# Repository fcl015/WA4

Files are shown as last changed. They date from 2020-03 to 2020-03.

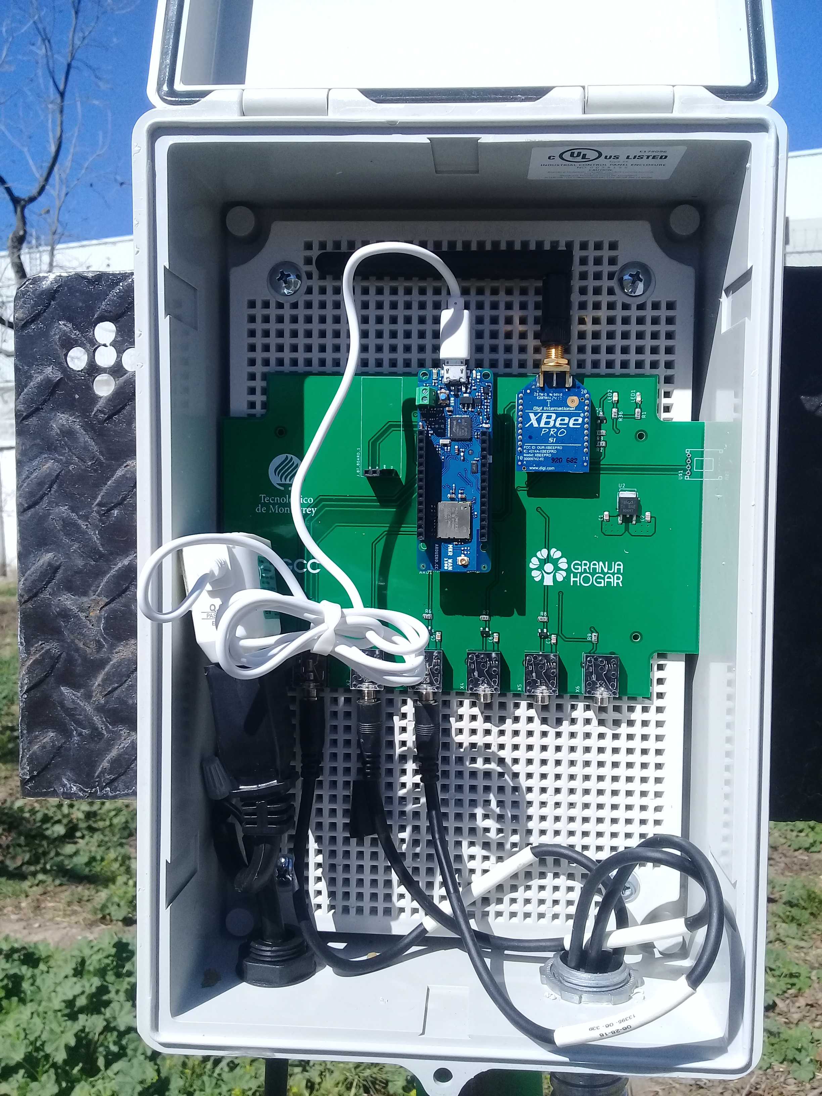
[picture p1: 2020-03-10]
03_Documentos/Fotos/2019-01/20190207_122751.jpg

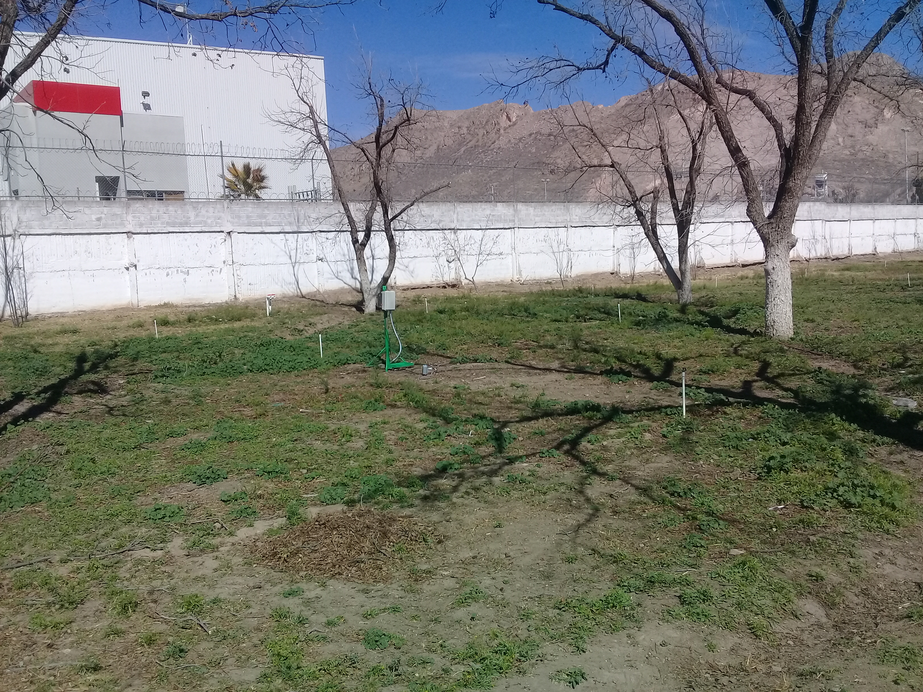
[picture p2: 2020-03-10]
03_Documentos/Fotos/2019-01/20190207_122912.jpg

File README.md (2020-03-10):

# WA4

Plataforma Tecnológica para Riego de Precisión
Se ha desarrollado y validado en campo una plataforma tecnológica para el manejo eficiente en la distribución y el consumo de agua en sistemas de riego agrícola y de áreas verdes. La plataforma ofrece servicios de internet de las cosas, medición, control, predicción y supervisión para una red de riego inteligente capaz de manejar restricciones de infraestructura (agua y energía limitada) valorando las condiciones ambientales (radiación solar, temperatura, lluvia, evapotranspiración) y del cultivo (humedad de suelo, desarrollo vegetativo).  
Actualmente la plataforma se encuentra instalada en una huerta Nogalera y en un invernadero. Experimentalmente, se han obtenido resultados de ahorro de agua entre 30%-40% y de reducción de consumo de energía de entre 20%-30% con respecto a los sistemas de riego automatizados utilizados en la región.
La plataforma consta de tres productos: (1) Crop.Net para monitoreo de humedad de suelo y desarrollo vegetativo, (2) Weather.Net para monitoreo de condiciones ambientales, y (3) Water.Net para control de riego y fertilizantes. Estos productos son modulares y escalables para ajustarse a las necesidades del cliente y al tamaño de las áreas de cultivo.

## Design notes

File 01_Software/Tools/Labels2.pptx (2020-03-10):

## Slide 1

Nodo Climático
Xbee: 0013A20040B135BC
Bluetooth: CLIMA

Nodo Sensor
Xbee: 0013A200416CC8A3
Bluetooth: AREA01

Nodo Sensor
Xbee: 0013A200416CC89C
Bluetooth: AREA02

Nodo Sensor
Xbee: 0013A200416CC899
Bluetooth: AREA03

Nodo Sensor
Xbee: 0013A200416CC89B
Bluetooth: AREA04

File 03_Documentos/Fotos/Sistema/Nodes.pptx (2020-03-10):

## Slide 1

Unidad Microcontroladora
SAMD21 Cortex-M0+ 32bit low power ARM

Blue-tooth
comm

Fuente de Poder

Zigbee comm

Nodo Sensor

LoRa comm

GPS

Unidad Microcontroladora
SAMD21 Cortex-M0+ 32bit low power ARM

Blue-tooth
comm

Fuente de Poder

Zigbee comm

Nodo Actuador

LoRa comm

GPS

Acondicio-namiento de entrada

Acondicio-namiento de entrada

Acondicio-namiento de salida

Sensor 1

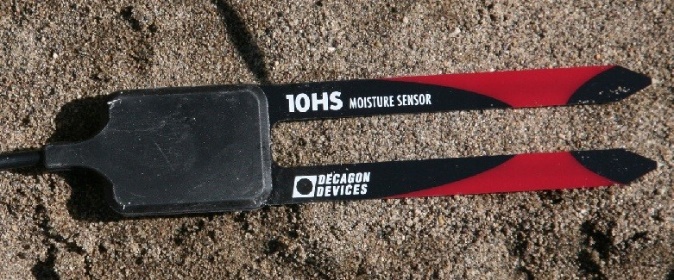
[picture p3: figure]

Sensor Flujo

Válvula

Sensor 2

Sensor 3

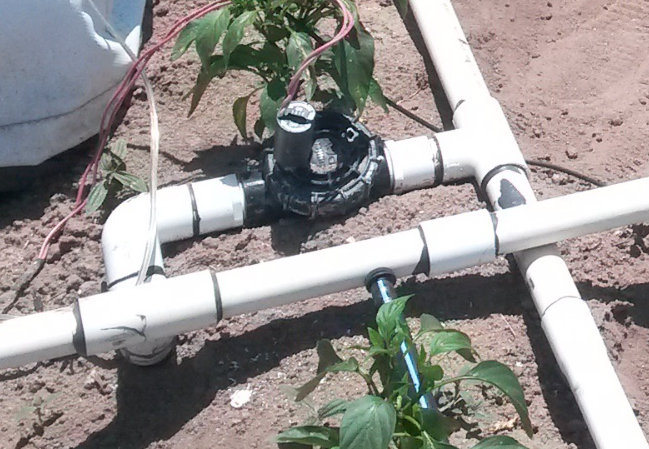
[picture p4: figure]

NDVI field

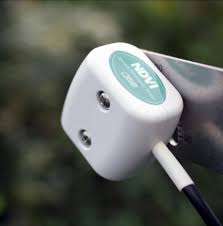
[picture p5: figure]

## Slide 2

Unidad Microcontroaldora
SAMD21 Cortex-M0+ 32bit low power ARM

Nodo Climático

LoRa comm

Nodo Controlador

Raspberry Pi 3B+
(Bradcom BCM2837Bo quad-core A53, 64bits, 1.4 GHz)

Blue-tooth
comm

Fuente de Poder

Zigbee comm

GPS

Blue-tooth
comm

Fuente de Poder

Zigbee comm

NIR Camera

WiFi
comm

Acondicio-namiento de entrada

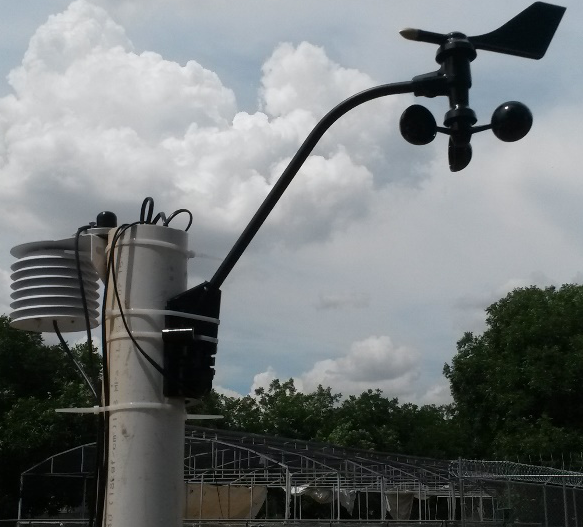
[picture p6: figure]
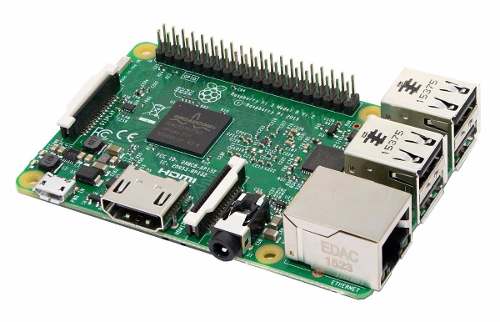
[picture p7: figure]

Davis Cup

PYR Sensor

NDVI Hem

VP-4

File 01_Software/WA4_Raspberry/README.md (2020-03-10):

# WA4_Raspberry
# Updated Sep-2019

Directories:

bin 	- python executable programs
config 	- csv configuration files
data 	- latest data from sensors and actuators
log 	- output log files
scripts - scripts for crontab and boot
tools	- program tools to check communication with nodes
www	- web interface (OLD webiopi)
www_flask - web interface (NEW flask)

Files

bin\control_loop_area1.py	- main file for irrigation area 1
bin\control_loop_area2.py	- main file for irrigation area 2
bin\control_loop_area3.py	- main file for irrigation area 3
bin\control_loop_area4.py	- main file for irrigation area 4
bin\wa_config_data.py		- functions to access configuration files
bin\wa_control.py		- functions for control and data fusion algorithms
bin\wa_xbee_comm.py		- function for Zigbee communication
bin\wa_iot_comm.py		- function for IoT interface (ThingSpeak)

config\config_area1.csv		- configuration file for irrigation area 1
config\config_area2.csv		- configuration file for irrigation area 2
config\config_area3.csv		- configuration file for irrigation area 3
config\config_area4.csv		- configuration file for irrigation area 4
config\manual_control_area1.csv	- configuration file for manual irrigation area 1
config\manual_control_area2.csv	- configuration file for manual irrigation area 2
config\manual_control_area3.csv	- configuration file for manual irrigation area 3
config\manual_control_area4.csv	- configuration file for manual irrigation area 4
config\sched_area1.csv		- configuration file for scheduling irrigation area 1
config\sched_area2.csv		- configuration file for scheduling irrigation area 2
config\sched_area3.csv		- configuration file for scheduling irrigation area 3
config\sched_area4.csv		- configuration file for scheduling irrigation area 4
config\operation_mode_area1.csv	- confirguration file for operation mode area 1
config\operation_mode_area2.csv	- confirguration file for operation mode area 2
config\operation_mode_area3.csv	- confirguration file for operation mode area 3
config\operation_mode_area4.csv	- confirguration file for operation mode area 4

log\crontab.txt			- log data for coontab services
log\video.txt			- log data for video server
log\webiopi.txt			- log data for webiopi server
log\webfalsk.txt		- log data for flask server

scripts\cron.txt		- cron process definition, start each irrigation area monitoring every 5 minutes
scripts\start_crontab.sh	- script to start crontab process (once executed, onlye removed by command. crontab -r
scripts\start_mjpg_streamer.sh	- start video server during startup (boot), to configure file must be copied to directory /etc/init.d/
scripts\start_webiopi.sh	- (OLD)start web server during startup (boot), to configure file must be copied to directory /etc/init.d/
scripts\start_WebFlaskServer.sh	- (NEW)start web falsk server during startup (boot), to configure file must be copied to directory /etc/init.d/
scripts\start_WA4_Raspberry_All_Areas.sh	-execute monitor and control for all areas
scripts\start_WA4_Raspberry_Area1.sh		-execute monitor and control for area 1
scripts\start_WA4_Raspberry_Area2.sh		-execute monitor and control for area 2
scripts\start_WA4_Raspberry_Area3.sh		-execute monitor and control for area 3
scripts\start_WA4_Raspberry_Area4.sh		-execute monitor and control for area 4

tools\actuator_message.py	- Program to check communication with actuator node
tools\sensor_message.py		- Program to check communication with sensor node
tools\weather_message.py	- Program to check communication with weather node

www\html\			- (OLD) webiopi web pages for WA interface
www\python\scripts.py		- (OLD) main script to extract data from config, data and scripts directories

www\html\log_area1.csv		- output log data for irrigation area 1
www\html\log_area2.csv		- output log data for irrigation area 2
www\html\log_area3.csv		- output log data for irrigation area 3
www\html\log_area4.csv		- output log data for irrigation area 4

www_flask\runWebServer.py	- (NEW) Main flask program
www_flask\wa4_functions.py	- (NEW) Complementary flask functions
www_flask\static\		- (NEW) Javascript and css files
www_flask\templates\		- (NEW) HTML files for flask

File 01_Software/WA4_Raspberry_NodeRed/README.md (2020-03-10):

# WA4_Raspberry
# Updated Sep-2019

Directories:

bin 	- python executable programs
config 	- csv configuration files
data 	- latest data from sensors and actuators
log 	- output log files
scripts - scripts for crontab and boot
tools	- program tools to check communication with nodes
www_flask - web interface

Files

bin\control_loop_area1.py	- main file for irrigation area 1
bin\control_loop_area2.py	- main file for irrigation area 2
bin\control_loop_area3.py	- main file for irrigation area 3
bin\control_loop_area4.py	- main file for irrigation area 4
bin\wa_config_data.py		- functions to access configuration files
bin\wa_control.py		- functions for control and data fusion algorithms
bin\wa_xbee_comm.py		- function for Zigbee communication
bin\wa_iot_comm.py		- function for IoT interface (ThingSpeak)

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

data\data_area1.csv		- Current data for irrigation area 1
data\data_area2.csv		- Current data for irrigation area 2
data\data_area3.csv		- Current data for irrigation area 3
data\data_area4.csv		- Current data for irrigation area 4

log\crontab.txt			- log data for coontab services
log\video.txt			- log data for video server
log\webiopi.txt			- log data for webiopi server
log\webfalsk.txt		- log data for flask server

scripts\cron.txt		- cron process definition, start each irrigation area monitoring every 5 minutes
scripts\start_crontab.sh	- script to start crontab process (once executed, onlye removed by command. crontab -r
scripts\start_mjpg_streamer.sh	- start video server during startup (boot), to configure file must be copied to directory /etc/init.d/
scripts\start_WebFlaskServer.sh	- start web falsk server during startup (boot), to configure file must be copied to directory /etc/init.d/
scripts\start_WA4_Raspberry_All_Areas.sh	-execute monitor and control for all areas
scripts\start_WA4_Raspberry_Area1.sh		-execute monitor and control for area 1
scripts\start_WA4_Raspberry_Area2.sh		-execute monitor and control for area 2
scripts\start_WA4_Raspberry_Area3.sh		-execute monitor and control for area 3
scripts\start_WA4_Raspberry_Area4.sh		-execute monitor and control for area 4

tools\actuator_message.py	- Program to check communication with actuator node
tools\sensor_message.py		- Program to check communication with sensor node
tools\weather_message.py	- Program to check communication with weather node

www_flask\runWebServer.py	- Main flask program
www_flask\wa4_functions.py	- Complementary flask functions
www_flask\static\		- Javascript and css files
www_flask\templates\		- HTML files for flask
www_flask\wa4_log\log_area1.csv	- Historic data for irrigation area 1
www_flask\wa4_log\log_area2.csv	- Historic data for irrigation area 2
www_flask\wa4_log\log_area3.csv	- Historic data for irrigation area 3
www_flask\wa4_log\log_area4.csv	- Historic data for irrigation area 4

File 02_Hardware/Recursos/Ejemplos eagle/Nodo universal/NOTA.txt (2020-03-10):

Este nunca se fabricó, ni siquiera en prototipo, por lo que nunca se probó su correcto funcionamiento.

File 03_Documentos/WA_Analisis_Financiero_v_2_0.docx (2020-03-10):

# Análisis Financiero

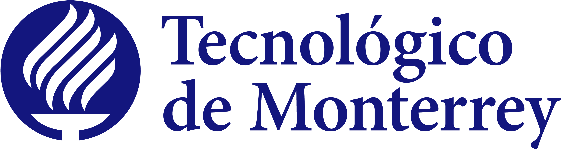
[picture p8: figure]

Plataforma Tecnológica de Riego de Precisión Agrícola y de Áreas Verdes

# Documento: Análisis de costos y viabilidad financiera

# Proyecto: CHIH-2018-C03-194128

Revisión: 2.0

Fecha: Diciembre 2018

Resumen: Este documento describe análisis financiero del proyecto de “Plataforma Tecnológica de Riego de Precisión Agrícola y de Áreas Verdes”. El objetivo del proyecto es diseñar e implementar un prototipo de riego automatizado para grandes extensiones territoriales, con la finalidad de reducir el consumo del agua y mejorar la eficiencia del cultivo.

# Keywords: análisis financiero, agricultura de precisión, automatización, eficiencia del agua.

El contenido de este documento no se considera oferta, propuesta o acuerdo, sino hasta que sea confirmado en documento por escrito que contenga la firma autógrafa del apoderado legal del ITESM. El contenido de este documento es confidencial y se entiende dirigido y para uso exclusivo del destinatario, por lo que no podrá distribuirse y/o difundirse por ningún medio sin la previa autorización del emisor original. Si usted no es el destinatario, se le prohíbe su utilización total o parcial para cualquier fin.

# HISTORIA DE REVISIONES

Rev. No. | Fecha | Autor | Comentarios
1.0 | Junio, 2015 | Sergio Gallegos / Camilo Lozoya | Versión original del documento.
2.0 | Diciembre, 2018 | Camilo Lozoya | Nueva revisión, proyecto Chihuahua Sustentable

Contenido

# 1. Introducción

## 1.1 Alcance

El documento de Análisis Financiero describe la viabilidad económica para una potencial implementación comercial del producto tecnológico desarrollado en el proyecto de “Automatización para el uso eficiente del agua en sistemas de riego agrícola”.

## 1.2 Propósito

Este proyecto tiene como objetivo desarrollar un eficiente sistema de riego agrícola para grandes extensiones territoriales, mediante la implementación de un sistema automatizado en tiempo real, que permita utilizar solamente la cantidad de agua necesaria, en el momento adecuado y en el lugar correcto. Teniendo como beneficio principal el incremento de la eficiencia en el uso del agua, es decir producir más cultivos con menos cantidad de agua.

Este documento tiene como propósito de analizar la viabilidad económica para una potencial implementación comercial del producto tecnológico desarrollado en el proyecto de “Automatización para el uso eficiente del agua en sistemas de riego agrícola”.

## 1.3 Financiamiento del Proyecto

Este proyecto es financiado por el Fondo Mixto de Fomento a la Investigación Científica y Tecnológica CONACyT – Gobierno del Estado de Chihuahua, en conjunto con el Instituto Tecnológico y de Estudios Superiores de Monterrey, Campus Chihuahua. También se obtuvo financiamiento de Grupo Cementos de Chihuahua a través de su iniciativa “Construyamos un Chihuahua Sustentable”.

## 1.4 Resumen Ejecutivo

En el estado de Chihuahua se registra una precipitación promedio anual muy baja (inferior a 420 mm), lo que lo ubica entre las primeras cuatro entidades federativas que registran las precipitaciones más bajas a nivel nacional. Debido a esto, la cantidad de agua disponible es generalmente insuficiente para cubrir las necesidades de uso cotidiano, e impacta seriamente en la recarga de cuerpos de agua y acuíferos subterráneos. Adicionalmente Chihuahua ha sido afectado por eventos de sequía, ocasionando pérdidas considerables principalmente en el sector agropecuario y forestal. Algunos de los factores que hacen que cada día crezca la vulnerabilidad a la sequía, son: los procesos de urbanización, el crecimiento poblacional, el desarrollo de la agricultura, ganadería e industria, el mayor consumo de energía, los mayores requerimientos de agua para consumo humano, y la reducción en la disponibilidad de agua de la calidad requerida para ciertos usos.

El concepto de “uso eficiente de agua” incluye cualquier medida que reduzca la cantidad que se utiliza por unidad de cualquier actividad, y que favorezca el mantenimiento o mejoramiento de la calidad del agua. Específicamente el sector agrícola representa el mayor consumidor de agua en Chihuahua, ya que se estima que requiere alrededor del 85% del agua disponible. Deficiencias en la extracción, conducción y uso del agua, son las mayores causantes del desperdicio de este vital líquido y de la insuficiencia de humedad en el suelo que reduce o nulifica el desarrollo vegetativo.

Actualmente, los sistemas de irrigación automáticos ofrecidos por el mercado al sector agrícola, se basan en la definición de períodos de tiempo para el uso de agua de riego, sin embargo no se consideran otros factores como humedad de la tierra, salinidad del suelo, intensidad de la luz solar, temperatura ambiente, necesidad de agua por parte del cultivo, entre otros. Por la tanto la eficiencia lograda por estos sistemas puede ser mejorada al considerar todos los elementos críticos que conforman un proceso de irrigación. Se estima que el promedio mundial de eficiencia en el uso del agua, aún con estos sistemas, es de entre un 40% a un 50%. Es decir, entre el 60% a 50% del agua de riego se desperdicia.

Los principales beneficios que se obtendrán a partir de la implementación del proyecto son:

- Incrementar la eficiencia en el uso de agua en comparación con los sistemas actuales de riego agrícola.
- Reducir el consumo de energía eléctrica utilizado en los sistemas de riego actuales.
- Detectar oportunamente fugas de agua y fallas en general del sistema de riego, mediante un sistema de monitoreo y supervisión.

La realización de este proyecto requiere un enfoque multidisciplinario, por lo que se formarán tres equipos de trabajo: (1) equipo de procesos de riego y uso de suelos de cultivo, (2) equipo de control y adquisición de datos, y (3) equipo de sistemas de información y comunicación de datos. Como resultado final del proyecto se implementará un prototipo funcional de un sistema de riego automático con información de tiempo real capaz de proveer sus servicios en al menos una hectárea de suelo agrícola. El prototipo debe ser capaz de demostrar en campo los beneficios que ofrece el proyecto.

## 1.5 Definiciones y acrónimos

### 1.5.1 Acrónimos

Acrónimo | Descripción
QFD | Quality Function Deployment
DFMEA | Design Failure Mode and Effect Analysis

# 2. Arquitectura del Sistema

## 2.1 Descripción

La arquitectura del sistema modular de adquisición de datos tiene como objetivo la flexibilidad de poder agregar o quitar componentes sin afectar la funcionalidad individual de los elementos, pero con la posibilidad de ir consolidando la información y poderla acceder desde distintos niveles. La arquitectura propuesta, como se muestra en la Fig. 1, se divide en tres niveles de acceso: nivel autónomo (stand-alone), nivel red local (local network), y nivel red global (global network).

Figura 1: Arquitectura del sistema dividida en tres capas físicas.

## 2.2 Nivel Autónomo

Cada módulo autónomo tiene la capacidad tanto de obtener mediciones de sensores como activar dispositivos actuadores, también puede almacenar información histórica del comportamiento de los sensores y actuadores en una memoria no volátil. Se utiliza una memoria tipo MicroSD , debido a su tamaño pequeño y su bajo consumo de energía, a través de un adaptador MicroSD-USB (Universal Serial Bus) la información contenida puede ser accedida fuera de línea por una computadora personal.

Cada uno de los módulos del nivel autónomo, independientemente de su función específica, se compone de los elementos mostrados en la Fig. 2.

Fig. 2: Diseño de hardware del módulo de nivel autónomo

La fuente de alimentación consta de una batería recargable de 12 volts, que puede estar conectada a un panel solar para una recarga continua, o puede recargarse periódicamente fuera de línea mediante un cargador externo. La tarjeta microcontrolador utilizada es Arduino Uno (http://www.arduino.cc) que incluye un microcontrolador de bajo costo ATmega328. Los dispositivos sensores se conectan al módulo mediante un circuito de acondicionamiento de entrada con 5 puertos, cada puerto de entrada puede configurarse independientemente para aceptar hasta tres tipos de señales diferentes: señales analógicas continuas, señales de pulsos y señales digitales basadas en el protocolo SDI-12 (Serial Digital Interface at 1200 baud, http://www.sdi-12.org/). El módulo cuenta con dos puertos de salidas para conectar dispositivos actuadores, las salidas son del tipo de relevadores de estado sólido capaces de manejar señales de corriente alterna y de corriente directa. El módulo de comunicación inalámbrica se implementa mediante un transmisor-receptor de radiofrecuencia Xbee (http://www.digi.com) operando a 2.4 Ghz, con una velocidad de 9600 bps y un alcance de 1.6 kms en campo abierto, la comunicación inalámbrica permite al módulo autónomo operar en modo red local, al tener la capacidad de enviar información al módulo central. Finalmente, se cuenta con un dispositivo de almacenamiento MicroSD utilizado en su modalidad autónoma.

## 2.3 Nivel Red Local

En el nivel red local se implementa una red de sensores inalámbrica para consolidar la información de diferentes sensores, ubicados en diferentes localidades, en un solo módulo de concentración de datos o módulo central. La red de corto alcance se implementa sobre el protocolo IEEE 802.15.4 que se ha convertido en el estándar de-facto para el monitoreo de variables ambientales, debido a su bajo costo, bajo consumo de potencia y baja velocidad de transmisión. En este nivel de acceso se puede obtener información consolidada a partir de las mediciones directas de los sensores, como es el cálculo de la evapotranspiración de referencia a partir de variables ambientales, o donde se obtiene un valor representativo de humedad de suelo a partir de múltiples sensores ubicados a lo largo de un área de riego de gran extensión. En el nivel de red local los datos obtenidos, incluyendo la información consolidada, pueden ser visualizados directamente en una computadora personal que tenga acceso a la red local.

El módulo central se compone de un microcontrolador de alto rendimiento dsPIC33F dentro de la tarjeta de Microchip Explorer 16 (http://www.microchip.com/), ver Fig. 3. El módulo tiene la capacidad de comunicarse con los módulos autónomos mediante la red de corto alcance. Además tiene la capacidad además tiene la capacidad de comunicación a larga distancia con el servidores de datos por medio del protocolo de comunicación GPRS, implementado por el circuito SIM900 (SIMComm http://www.sim.com/). De esta manera el módulo central sirve como un puente de enlace entre un grupo de sensores y actuadores ubicados en una región específica con la red global de internet. Si no se desea el acceso a internet, la información consolidada por el módulo central puede ser accesada por medio de una computadora personal a través de la red de corto alcance.

Fig. 3: Diseño de hardware del módulo central.

## 2.4 Nivel Red Global

En el nivel de red global la información de uno o más módulos centrales es almacenada en un servidor de datos con acceso a internet. El servidor cuenta con una base de datos para almacenar la información histórica, cabe mencionar que el servidor puede ser propietario o se pueden utilizar servidores de terceros que ofrecen una plataforma de servicios de almacenamiento y acceso de información vía internet, como la plataforma Xively. La comunicación entre los módulos centrales y el servidor se realiza mediante el protocolo de comunicación para telefonía celular GPRS (General Packet Radio Service), ya que este medio presenta actualmente un alto nivel de cobertura a nivel mundial. GPRS es un servicio de datos móviles orientado a paquetes utilizado por los sistemas GSM (Global System for Mobile Communications) y es un adecuado puente de comunicación entre redes de sensores inalámbricas e internet [17]. El usuario en este nivel puede acceder a la información a través de páginas de internet o aplicaciones que tengan acceso a internet desde cualquier lugar.

El módulo servidor se compone incluye un sistema de multinúcleo proporcionado por el servidor Dell PowerEdge (http://www.dell.com/), el cual incluye servicios web, acceso a internet y una base de datos para almacenar información histórica proveniente de múltiples nodos centrales, ubicados en cualquier región, como se muestra en la Fig. 4. La base de datos se implementa mediante la plataforma libre Django (https://www.djangoproject.com/). Si no se desea un servidor propio, pero si se desea tener acceso al sistema mediante internet, se puede utilizar la plataforma Xively de manera gratuita.

Fig. 3: Diseño de hardware del servidor de datos.

# 3. Análisis Financiero

## 3.1 Lista de Materiales

Se realizó un resumen de los materiales principales a usarse durante el proyecto, al igual que sus precios en pesos y dólares según la venta de este. Igualmente se calculó un análisis de costos para cada módulo usado, agregando el resumen de piezas y costo de cada una de ellas.

### 3.1.1 Materiales Generales

### 3.1.2 Módulo Actuador

### 3.1.3 Módulo Sensor-Climático

## 3.2 Costo Comercial por Módulo Sensor

Material | 140.00 | 2,800.00
Cargadores/Baterias | 10.00 | 200.00
Gabinete | 45.00 | 900.00
Caja | 20.00 | 400.00
PCB | 35.00 | 700.00
Zigbee+Bluetooth | 50.00 | 1,000.00
TOTAL MATERIAL | 300.00 | 6,000.00
Profit | 350.00 | 7,000.00
Sensores SM | 600.00 | 12,000.00
Instalación | 100.00 | 2,000.00
Costo Comercial Total | 1,250.00 | 25,000.00

## 3.3 Costo Comercial por Módulo Actuador

| Dollars | Pesos
Material | 140.00 | 2,800.00
Cargadores/Baterias | 10.00 | 200.00
Gabinete | 45.00 | 900.00
Caja | 20.00 | 400.00
PCB | 35.00 | 700.00
Zigbee+Bluetooth | 50.00 | 1,000.00
TOTAL MATERIAL | 300.00 | 6,000.00
Profit | 350.00 | 7,000.00
Sensores SM | 600.00 | 12,000.00
Instalación | 100.00 | 2,000.00
Costo Comercial Total | 1,250.00 | 25,000.00

## 3.4 Costo Comercial por Módulo Climático

| Dollars | Pesos
Material | 140.00 | 2,800.00
Cargadores/Baterias | 10.00 | 200.00
Gabinete | 45.00 | 900.00
Caja | 20.00 | 400.00
PCB | 35.00 | 700.00
Zigbee+Bluetooth | 50.00 | 1,000.00
TOTAL MATERIAL | 300.00 | 6,000.00
Profit | 350.00 | 7,000.00
Sensores Weather | 1,600.00 | 32,000.00
Instalación | 100.00 | 2,000.00
Costo Comercial Total | 2,250.00 | 45,000.00

## 3.5 Costo Comercial Total por 4 Áreas de Riego

| | Costo Unitario | | Costo Total
Cantidad | Módulo | Dollars | Pesos | Dollars | Pesos
4 | Módulos Sensores | 1,250.00 | 25,000.00 | 5,000.00 | 100,000.00
1 | Módulo Climático | 2,250.00 | 45,000.00 | 2,250.00 | 45,000.00
1 | Módulo Actuador | 1,250.00 | 25,000.00 | 1,250.00 | 25,000.00
1 | Módulo Controlador | 0.00 | 0.00 | 0.00 | 0.00
| Costo Comercial Total | | | 8,500.00 | 170,000.00

# 4. Análisis Cualitativos

## 4.1 QFD (Quality Function Deployment)

Se evaluó el proyecto según las necesidades del cliente. La siguiente tabla muestra el método el método de gestión de calidad según las demandas del usuario final llamado QFD. Lo usamos para saber las necesidades del cliente y tener la idea de que componentes usar (Figura 4).

## 4.2 DFMEA (Design Failure Mode & Effect Analysis)

Se realizó un método para detector fallas comunes en el sistema, este método nos dio un mejor control en la instalación y producción del sistema completo, a continuación se muestran las tablas.

INFORMACIÓN USO INTERNP COPYRIGHT © 2018, INSTITUTO TECNOLÓGICO Y DE ESTUDIOS SUPERIORES DE MONTERREY

Página 2 of 20 INFORMACIÓN USO INTERNo COPYRIGHT © 2018, INSTITUTO TECNOLÓGICO Y DE ESTUDIOS SUPERIORES DE MONTERREY

Análisis Financiero CHIH-2018-C03-194128

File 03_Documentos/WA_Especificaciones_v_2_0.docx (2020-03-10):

# Especificaciones Funcionales

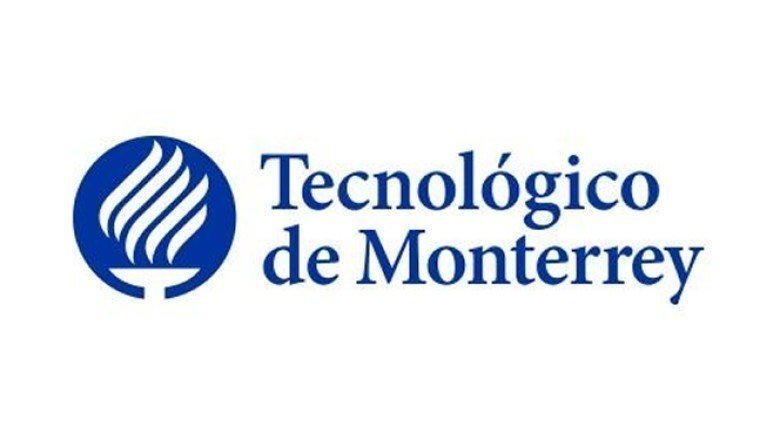
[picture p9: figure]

Plataforma Tecnológica de Riego de Precisión Agrícola y de Áreas Verdes

# Documento: Requerimientos / Especificaciones Funcionales

# Proyecto: CHIH-2018-C03-194128

Revisión: 2.0

Fecha: Diciembre 2018

Resumen: Este documento describe las especificaciones o requerimientos funcionales del sistema propuesto en el proyecto de “Plataforma Tecnológica de Riego de Precisión Agrícola y de Áreas Verdes”. El objetivo del proyecto es diseñar e implementar un prototipo de riego automatizado para grandes extensiones territoriales, con la finalidad de reducir el consumo del agua y mejorar la eficiencia del cultivo.

# Keywords: Requerimientos, especificación, agricultura, automatización, eficiencia del agua.

El contenido de este documento no se considera oferta, propuesta o acuerdo, sino hasta que sea confirmado en documento por escrito que contenga la firma autógrafa del apoderado legal del ITESM. El contenido de este documento es confidencial y se entiende dirigido y para uso exclusivo del destinatario, por lo que no podrá distribuirse y/o difundirse por ningún medio sin la previa autorización del emisor original. Si usted no es el destinatario, se le prohíbe su utilización total o parcial para cualquier fin.

# HISTORIA DE REVISIONES

Rev. No. | Fecha | Autor | Comentarios
1.0 | Septiembre, 2013 | Camilo Lozoya | Versión original del documento.
1.1 | Diciembre, 2013 | Camilo Lozoya | Revisión previa al primer reporte de avances
1.2 | Junio, 2014 | Camilo Lozoya | Revisión previa al segundo reporte de avances
1.3 | Junio, 2015 | Camilo Lozoya | Reporte final
2.0 | Diciembre, 2018 | Camilo Lozoya | Nueva revisión, proyecto Chihuahua Sustentable

Contenido

# 1. Introducción

## 1.1 Alcance

Las especificaciones funcionales del sistema definen las características que el prototipo debe tener con la finalidad de cumplir los objetivos del proyecto. Las especificaciones funcionales toman como base la arquitectura del sistema, y en conjunto con este establecen los lineamientos a seguir en el diseño modular del proyecto “Automatización para el uso eficiente del agua en sistemas de riego agrícola”.

## 1.2 Propósito

Este documento tiene como propósito describir los requerimientos funcionales del sistema. Se entiende por requerimiento funcional a los servicios que debe de ofrecer el sistema desde la perspectiva del usuario.

## 1.3 Financiamiento del proyecto

Este proyecto es financiado por el Fondo Mixto de Fomento a la Investigación Científica y Tecnológica CONACyT – Gobierno del Estado de Chihuahua, en conjunto con el Instituto Tecnológico y de Estudios Superiores de Monterrey, Campus Chihuahua. También se obtuvo financiamiento de Grupo Cementos de Chihuahua a través de su iniciativa “Construyamos un Chihuahua Sustentable”.

## 1.4 Resumen Ejecutivo

En el estado de Chihuahua se registra una precipitación promedio anual muy baja (inferior a 420 mm), lo que lo ubica entre las primeras cuatro entidades federativas que registran las precipitaciones más bajas a nivel nacional. Debido a esto, la cantidad de agua disponible es generalmente insuficiente para cubrir las necesidades de uso cotidiano, e impacta seriamente en la recarga de cuerpos de agua y acuíferos subterráneos. Adicionalmente Chihuahua ha sido afectado por eventos de sequía, ocasionando pérdidas considerables principalmente en el sector agropecuario y forestal. Algunos de los factores que hacen que cada día crezca la vulnerabilidad a la sequía, son: los procesos de urbanización, el crecimiento poblacional, el desarrollo de la agricultura, ganadería e industria, el mayor consumo de energía, los mayores requerimientos de agua para consumo humano, y la reducción en la disponibilidad de agua de la calidad requerida para ciertos usos.

El concepto de “uso eficiente de agua” incluye cualquier medida que reduzca la cantidad que se utiliza por unidad de cualquier actividad, y que favorezca el mantenimiento o mejoramiento de la calidad del agua. Específicamente el sector agrícola representa el mayor consumidor de agua en Chihuahua, ya que se estima que requiere alrededor del 85% del agua disponible. Deficiencias en la extracción, conducción y uso del agua, son las mayores causantes del desperdicio de este vital líquido y de la insuficiencia de humedad en el suelo que reduce o nulifica el desarrollo vegetativo.

Actualmente, los sistemas de irrigación automáticos ofrecidos por el mercado al sector agrícola, se basan en la definición de períodos de tiempo para el uso de agua de riego, sin embargo no se consideran otros factores como humedad de la tierra, salinidad del suelo, intensidad de la luz solar, temperatura ambiente, necesidad de agua por parte del cultivo, entre otros. Por la tanto la eficiencia lograda por estos sistemas puede ser mejorada al considerar todos los elementos críticos que conforman un proceso de irrigación. Se estima que el promedio mundial de eficiencia en el uso del agua, aún con estos sistemas, es de entre un 40% a un 50%. Es decir, entre el 60% a 50% del agua de riego se desperdicia.

Los principales beneficios que se obtendrán a partir de la implementación del proyecto son:

- Incrementar la eficiencia en el uso de agua en comparación con los sistemas actuales de riego agrícola.
- Reducir el consumo de energía eléctrica utilizado en los sistemas de riego actuales.
- Detectar oportunamente fugas de agua y fallas en general del sistema de riego, mediante un sistema de monitoreo y supervisión.

La realización de este proyecto requiere un enfoque multidisciplinario, por lo que se formarán tres equipos de trabajo: (1) equipo de procesos de riego y uso de suelos de cultivo, (2) equipo de control y adquisición de datos, y (3) equipo de sistemas de información y comunicación de datos. Como resultado final del proyecto se implementará un prototipo funcional de un sistema de riego automático con información de tiempo real capaz de proveer sus servicios en al menos una hectárea de suelo agrícola. El prototipo debe ser capaz de demostrar en campo los beneficios que ofrece el proyecto.

## 1.5 Definiciones y acrónimos

### 1.5.1 Definiciones

Término | Definición
Evapotranspiración | Representa el agua perdida causada por la evaporación en la superficie de la tierra y por la transpiración del cultivo. Represents the water lost caused by soil surface evaporation and crop transpiration
Humedad de suelo | Se refiere a la cantidad de agua en la tierra, la cual se describe como el contenido volumétrico de agua.

### 1.5.2 Acrónimos

Acrónimo | Descripción
VWC | Contenido volumétrico de agua
ETo | Evapotranspiración de referencia.
MPC | Modelo de control predictivo
GSM | Estandard de comunicación para teléfonos celulares (Global System for Mobile Communication)

# 2. Descripción del Sistema

## 2.1 Módulos funcionales

La arquitectura del sistema se basa en la dinámica del proceso descrita y en el diseño del controlador propuesto, ambos descritos en la sección anterior. El objetivo del proyecto es definir, desarrollar e instalar un prototipo de un sistema de riego automático que sea capaz de incrementar la eficiencia del agua, reducir el consumo de energía eléctrica, mejorar la productividad del cultivo y detectar fallas en el sistema. En el diseño se considera la instalación y validación del prototipo en al menos una hectárea de cultivo.

El proyecto se divide en 3 módulos funcionales. La integración de los 3 módulos conforma el prototipo completo:

Módulo de proceso: este módulo incluye la identificación de sensores para mediciones en campo, la implementación de dispositivos de adquisición de datos. También se incluye el control de elementos actuadores como válvulas y bombas de agua. Las características de la red hidráulica, de la dinámica del proceso de riego forman parte de este módulo. Este módulo incluye la red de comunicación inalámbrica (red de corto alcance) entre sensores.

Módulo de control: este módulo se define las características del sistema de control, como variables de entrada, variables de salida y variables de estado. También se incluye la definición del algoritmo de control óptimo, así como el modelo matemático del sistema.

Módulo de comunicación y datos: este módulo define las características de la red de comunicación de datos de largo alcance. Se define la ubicación, potencia y confiabilidad de la transmisión-recepción de datos en forma inalámbrica. También se incluye la definición de una base de datos para almacenar información, así como las aplicaciones requeridas para interactuar con el sistema.

## 2.2 Niveles o capas del sistema

Desde una perspectiva física la arquitectura del sistema considera el desarrollo de tres capas o niveles físicos. Cada nivel está compuesto por un conjunto de dispositivos, cuya funcionalidad puede abarcar más de un módulo funcional. Así la capa física incluye los nodos sensores, nodos actuadores y nodos controladores del sistema, la capa de datos incluye los controladores, la base de datos y el servidor de datos, finalmente la capa de usuario se conforma principalmente por las aplicaciones que interactúan con los diferentes usuarios que puede tener el sistema (supervisor de riego, administrador del cultivo, investigador agrícola).

Capa Física: La capa física representa todos los elementos que se encuentran en contacto directo con el proceso. Estos elementos son un grupo de nodos distribuidos sobre la superficie de riego, en donde cada nodo tiene una función en específico. Los nodos se comunican entre sí, por medio de una red de sensores inalámbrica implementada por el protocolo Zigbee. Los nodos se clasifican en: controladores, sensores, actuadores, climáticos y repetidores.

Capa de Datos: La capa de datos se conforma de un servidor de cómputo con una base de datos. Esta capa interactúa con los nodos controladores del sistema de riego mediante una red de comunicación de largo alcance basada en el protocolo GSM/GPRS.

Capa de Usuario: La capa de usuarios se conforma de tres grupos de aplicaciones para que el usuario interactúe con el sistema automático de riego. La información que proveen las aplicaciones puede ser actual o histórica. El término usuario es utilizado en forma genérica para identificar a las personas o grupos de personas que pueden requerir información del proceso y del sistema de control. Los usuarios potenciales del sistema son: supervisores de riego, agricultores, administradores del negocio, investigadores agrícolas. Los tres tipos de aplicaciones disponibles en la capa del usuario son: (1) captura de datos, (2) monitoreo y supervisión, y (3) desempeño.

Figura 1: Arquitectura del sistema dividida en tres capas físicas.

# 3. Especificaciones Generales del Sistema

R.SIS.01 | El usuario puede seleccionar los tres modos de operación del sistema: manual, temporizado y automático.
R.SIS.02 | Se utiliza la red de internet para comunicar las aplicaciones del usuario con el servidor de datos.
R.SIS.03 | El esquema de comunicación entre las aplicaciones del usuario y el servidor de datos es de tipo cliente servidor.
R.SIS.04 | El servidor de datos se encuentra físicamente en un cuarto de cómputo con todas las facilidades necesarias (control de temperatura, respaldos, redundancia, acceso a internet, etc.)
R.SIS.05 | La base de datos se encuentra instalada en el servidor de datos.
R.SIS.06 | Existe un nodo controlador por cada área de riego.
R.SIS.07 | El sistema de riego está compuesto por una o varias áreas de riego.
R.SIS.08 | Para cada área de riego existe un cultivo en específico. Cada área de riego puede tener un cultivo diferente.
R.SIS.09 | La comunicación entre el controlador y servidor de datos se lleva a cabo por una red de largo alcance (red móvil GSM/GPRS)
R.SIS.10 | La comunicación entre el controlador y el servidor de datos es bidireccional y punto a punto.
R.SIS.11 | El esquema de comunicación del controlador al servidor de datos es de tipo periódico
R.SIS.12 | El esquema de comunicación del servidor de datos al controlador es de tipo esporádico.
R.SIS.13 | El controlador se comunica con los nodos sensores, actuadores, climáticos y repetidores por medio de una red de corto alcance (Zigbee).
R.SIS.14 | El esquema de comunicación entre el controlador y los nodos sensores, actuadores, climáticos y repetidores es del tipo maestro-esclavo y es peródico.
R.SIS.15 | Los nodos sensores, actuadores, climáticos y repetidores se encuentran alimentados eléctricamente por medio de energía fotovoltaica (celdas solares).
R.SIS.16 | Si el servidor de datos no está disponible el sistema de riego sigue funcionando, solamente no se reportan los datos, ni se puede cambiar el modo de operación.
R.SIS.17 | Los nodos mínimos necesarios para el funcionamiento del sistema son: nodo controlador, nodo sensor y nodo actuador.

# 4. Especificaciones funcionales por módulo

Las especificaciones funcionales se describen mediante los casos de uso. Un caso de uso es una descripción de los pasos o las actividades que deberán realizarse para llevar a cabo algún proceso. Los personajes o entidades que participarán en un caso de uso se denominan actores. En el contexto de ingeniería de software, un caso de uso es una secuencia de interacciones que se desarrollarán entre un sistema y sus actores en respuesta a un evento que inicia un actor principal sobre el propio sistema.

Los diagramas de casos de uso sirven para especificar la comunicación y el comportamiento de un sistema mediante su interacción con los usuarios y/u otros sistemas. O lo que es igual, un diagrama que muestra la relación entre los actores y los casos de uso en un sistema. Una relación es una conexión entre los elementos del modelo, por ejemplo la especialización y la generalización son relaciones. Los diagramas de casos de uso se utilizan para ilustrar los requerimientos del sistema al mostrar cómo reacciona a eventos que se producen en su ámbito o en él mismo.

## 4.1 Interface del Sistema

CASO DE USO | CU_USE_01
Nombre: | Configuración del Sistema
Descripción: | El usuario selecciona el modo de operación del sistema. Los modos de operación válidos son: Manual, Temporizado y Automático
Actor Primario: | Usuario del Sistema
Precondiciones: | El usuario ejecuta la aplicación de “Configuración del Sistema”
Curso Básico de Eventos: | 1. El usuario selecciona modo manual de operación a. Selecciona el área de riego b. Selecciona activación o desactivación de riego c. Confirma selección 2. El usuario selecciona modo temporizado de operación a. Selecciona área de riego b. Programa, modifica o cancela calendario de riego c. Confirma selección 3. El usuario selecciona modo automático de riego a. Selecciona área de riego b. Define nivel máximo de humedad de suelo (referencia) c. Define nivel mínimo de humedad de suelo (referencia) d. Programa, modifica o cancela restricciones de riego e. Confirma selección
Excepciones: | Error de comunicación
Supuestos: | Se asume que el área de riego es válida Se asume que el usuario conoce el tipo de cultivo en el área específica
Postcondiciones: | El modo de operación de un área de riego específica ha sido configurada

CASO DE USO | CU_USE_02
Nombre: | Monitoreo y Supervisión del Sistema
Descripción: | El usuario visualiza el estado de las áreas de riego y verifica la presencia o no de fallas o alarmas en el sistema
Actor Primario: | Usuario del Sistema
Precondiciones: | El usuario ejecuta la aplicación de “Monitoreo y Supervisión”
Curso Básico de Eventos: | 1. El usuario selecciona la opción de visualización del sistema a. Se despliega el modo de operación de cada área de riego b. Se despliega el estado actual de cada área de riego 2. El usuario selecciona la opción de verificación de alarmas y fallas a. Se despliega el tipo y ubicación de la falla o alarmas, si existen. b. Tipos de fallas y alarmas: Falla de comunicación Falla de medición Falla de activación Alarma por temperatura baja Alarma por falta de presión de agua
Excepciones: | Error de comunicación
Supuestos: | Se asume que el sistema es capaz de detectar fallas y alarmas
Postcondiciones: | El usuario conoce el estado del sistema

CASO DE USO | CU_USE_03
Nombre: | Desempeño del Sistema
Descripción: | El usuario visualiza el desempeño del sistema por área específica y periodo de tiempo.
Actor Primario: | Usuario del Sistema
Precondiciones: | El usuario ejecuta la aplicación de “Desempeño del Sistema”
Curso Básico de Eventos: | 1. El usuario selecciona el área de riego 2. El usuario selecciona el período de visualización 3. El usuario selecciona el tipo de gráfica a. Consumo de agua b. Consumo de energía eléctrica c. Evapotranspiración d. Humedad de suelo e. Factores climáticos f. Activación de riego
Excepciones: | Error de comunicación
Supuestos: | Se asume que el área de riego es válida Se asume que el usuario conoce el tipo de cultivo en el área específica
Postcondiciones: | El usuario visualiza el desempeño del sistema

## 4.2 Módulo de Comunicación y Datos

CASO DE USO | CU_DAT_01
Nombre: | Comunicación remota
Descripción: | El módulo de comunicación y datos recibe una transmisión remota de un módulo de control con la información actual de un área de riego específica: humedad de suelo, factores climáticos, flujo y presión de agua, activación/desactivación de riego, evapotranspiración de referencia.
Actor Primario: | Módulo de comunicación y datos
Precondiciones: | Módulo de control ha recibido y procesado información válida del proceso de riego de un área específica.
Curso Básico de Eventos: | 1. Módulo de control prepara la información 2. Módulo de control transmite la información utilizando una red de largo alcance 3. Módulo de comunicación recibe el paquete de datos. 4. Módulo de comunicación valida la integridad de los datos 5. Módulo de comunicación envía señal de recepción exitosa 6. Módulo de comunicación extrae la información relevantes del paquete 7. Módulo de comunicación almacena la información en la base de datos
Excepciones: | Falla de comunicación Base de datos sin capacidad de almacenar más información
Supuestos: | Se asume que la información enviada por el módulo de control es válida.
Postcondiciones: | La base de datos contiene la información más actualizada del área de riego específica.

CASO DE USO | CU_DAT_02
Nombre: | Configuración del controlador
Descripción: | El módulo de comunicación actualiza la configuración del modo de operación del controlador. Existen tres modos de operación válidos: Manual, Temporizado y Automático.
Actor Primario: | Módulo de comunicación y datos
Precondiciones: | El usuario ha seleccionado un área específica de riego y ha modificado se modo de operación y/o parámetros de funcionamiento.
Curso Básico de Eventos: | 1. Módulo de comunicación envía un paquete de datos al controlador de un área específica, con información del nuevo modo de operación y sus parámetros. a. Módo Manual: Activación o desactivación de riego. b. Modo Temporizado: Calendario de riego c. Modo Automático: Nivel máximo y mínimo de humedad de suelo, restricciones de riego. 2. Controlador recibe el mensaje y valida su contenido 3. Controlador envía señal de recepción exitosa. 4. Controlador reconfigura su modo de operación.
Excepciones: | Error de comunicación
Supuestos: | Se asume que el usuario selecciona un área de riego válida, un modo de operación y parámetros válidos.
Postcondiciones: | El controlador opera de acuerdo al nuevo modo de operación.

## 4.3 Módulo de Control

CASO DE USO | CU_CON_01
Nombre: | Variable del proceso
Descripción: | El módulo de control o controlador recibe información de la variable del proceso en el lazo de control (humedad de suelo).
Actor Primario: | Módulo de control
Precondiciones: | En el módulo de proceso, los nodos sensores se encuentran en funcionamiento y disponibles en la red de comunicación de corto alcance.
Curso Básico de Eventos: | 1. Controlador envía un mensaje a un nodo sensor específico (módulo de proceso) 2. Nodo sensor realiza la medición de humedad de suelo. 3. Nodo sensor envía el mensaje con la información de la humedad de suelo. 4. Controlador recibe el mensaje con la información. 5. Controlador repite los pasos 1 a 4, tantas veces como nodos sensores se encuentren disponibles en el módulo del proceso. 6. Controlador integra todas las lecturas en un solo valor.
Excepciones: | Error de comunicación Error de medición en el nodo sensor.
Supuestos: | Se asume que el controlador conoce el número de nodos sensores del módulo de proceso.
Postcondiciones: | El controlador tiene un valor que representa la humedad global de toda el área de riego.

CASO DE USO | CU_CON_02
Nombre: | Perturbación externa
Descripción: | El módulo de control o controlador recibe información de la perturbación externa actual. La perturbación externa representa el conjunto de todas las variables climáticas.
Actor Primario: | Módulo de control
Precondiciones: | En el módulo de proceso, los nodos climáticos se encuentran en funcionamiento y disponibles en la red de comunicación de corto alcance.
Curso Básico de Eventos: | 1. Controlador envía un mensaje a un nodo climático del módulo de proceso. 2. Nodo climático realiza las mediciones ambientales: humedad relativa, temperatura del aire, presión atmosférica, velocidad del viento, radiación solar. 3. Nodo sensor envía el mensaje con la información de las variables ambientales. 4. Controlador recibe el mensaje con la información. 5. Controlador calcula integra todos los valores ambientales en uno solo, a través del cálculo de la evapotranspiración de referencia.
Excepciones: | Error de comunicación Error de medición en el nodo climático.
Supuestos: | Se asume que el controlador conoce la fórmula para obtener la evapotranspiración.
Postcondiciones: | El controlador tiene un valor que representa la evapotranspiración de toda el área de riego.

CASO DE USO | CU_CON_03
Nombre: | Algoritmo de control
Descripción: | El controlador calcula la señal de control, mediante un algoritmo de control óptimo y predictivo, en base a la información de la variable del proceso (humedad de suelo) y la perturbación externa (evapotranspiración).
Actor Primario: | Módulo de control
Precondiciones: | El módulo de control tiene información actualizada de la humedad desuelo actual, el nivel de referencia de humedad de suelo, y la evapotranspiración. El módulo de control tiene el modelo matemático del proceso.
Curso Básico de Eventos: | 1. El controlador calcula el error actual: variable de proceso menos valor de referencia. 2. EL controlador aplica el error actual, la evapotranspiración al modelo matemático del proceso en forma iterativa, hasta obtener una señal de control óptima. 3. El controlador obtiene la señal de control óptima.
Excepciones: | Excepción durante el algoritmo de optimización.
Supuestos: | El modelo matemático del sistema es válido. Las reglas de optimización han sido previamente evaluadas.
Postcondiciones: | El controlador tiene disponible una señal de control que es óptima, para las condiciones actuales del proceso.

CASO DE USO | CU_CON_04
Nombre: | Señal de control
Descripción: | El módulo de control o controlador envía la señal de control de activar/desactivar el riego al nodo actuador (módulo de proceso).
Actor Primario: | Módulo de control
Precondiciones: | En el módulo de proceso, el nodo actuador se encuentra en funcionamiento y disponible en la red de comunicación de corto alcance. El controlador ha calculado la señal óptima de control.
Curso Básico de Eventos: | 1. Controlador prepara un mensaje con la señal de control. 2. El controlador envía un mensaje al nodo actuador. 3. El nodo actuador recibe el mensaje 4. El nodo actuador procesa la información del mensaje. 5. El nodo actuador envía al controlador un mensaje de operación exitosa.
Excepciones: | Error de comunicación Error de accionamiento en el nodo actuador.
Supuestos: | Se asume que el controlador tiene disponible una señal de control que es óptima, para las condiciones actuales del proceso.
Postcondiciones: | El nodo actuador tiene la señal de control actualizada.

## 4.4 Módulo de Proceso

CASO DE USO | CU_PRO_01
Nombre: | Medición de Humedad
Descripción: | El módulo de proceso realiza mediciones de humedad en zonas representativas del área de riego.
Actor Primario: | Módulo de proceso
Precondiciones: | Los sensores de humedad de suelo se encuentran instalados correctamente.
Curso Básico de Eventos: | 1. Recibe instrucción de inicio de lectura 2. Realiza la lectura del primer sensor 3. Almacena la información 4. Repite pasos 2 y 3 dependiendo del número de sensores conectados. 5. Conforma un paquete de datos con la información de las lecturas de datos.
Excepciones: | Error de medición en los sensores de humedad.
Supuestos: | Se asume que el módulo de proceso conoce el número de sensores conectados a cada nodo sensor.
Postcondiciones: | El módulo de proceso tiene disponible los valores de humedad de suelo en todas las zonas representativas del área de riego.

CASO DE USO | CU_PRO_02
Nombre: | Medición Climática
Descripción: | El módulo de proceso realiza mediciones climáticas en un único nodo en el área de riego.
Actor Primario: | Módulo de proceso
Precondiciones: | Los sensores de climáticos se encuentran instalados correctamente.
Curso Básico de Eventos: | 1. Recibe instrucción de inicio de lectura 2. Realiza la lectura del primer sensor 3. Almacena la información 4. Repite pasos 2 y 3 dependiendo del número de sensores conectados. 5. Conforma un paquete de datos con la información de las lecturas de datos.
Excepciones: | Error de medición en los sensores climáticos.
Supuestos: | Se asume que el módulo de proceso conoce el número y tipo de sensores climáticos conectados a cada nodo sensor.
Postcondiciones: | El módulo de proceso tiene disponible los valores climáticos actuales del área de riego.

CASO DE USO | CU_PRO_03
Nombre: | Accionamiento de válvulas
Descripción: | El módulo de proceso es capaz de accionar válvulas de flujo de agua para activar y desactivar el riego.
Actor Primario: | Módulo de proceso
Precondiciones: | Las válvulas se encuentran correctamente instaladas en el área de riego.
Curso Básico de Eventos: | 1. Recibe una instrucción de accionamiento. 2. Activa/desactiva la válvula de flujo 3. Confirma accionamiento exitoso. 4. Repite el paso 2 hasta completar el total de las válvulas
Excepciones: | Error accionamiento de válvulas.
Supuestos: | Se asume que el módulo de proceso conoce el número válvulas conectadas a cada nodo actuador.
Postcondiciones: | El módulo de proceso ha ejecutado el accionamiento de las válvulas en el área de riego.

CASO DE USO | CU_PRO_04
Nombre: | Accionamiento de bombas
Descripción: | El módulo de proceso es capaz de accionar bombas para proveer agua al sistema de riego.
Actor Primario: | Módulo de proceso
Precondiciones: | Las bombas se encuentran correctamente instaladas en el área de riego.
Curso Básico de Eventos: | 1. Recibe una instrucción de accionamiento. 2. Activa/desactiva la bomba de agua 3. Confirma accionamiento exitoso. 4. Repite el paso 2 hasta completar el total de bombas de agua.
Excepciones: | Error de accionamiento de las bombas.
Supuestos: | Se asume que el módulo de proceso conoce el número bombas conectadas a cada nodo actuador.
Postcondiciones: | El módulo de proceso ha ejecutado el accionamiento de las bombas de agua en el área de riego.

CASO DE USO | CU_PRO_05
Nombre: | Medición de flujo y presión
Descripción: | El módulo de proceso realiza mediciones de flujo y presión de agua en el área de riego.
Actor Primario: | Módulo de proceso
Precondiciones: | Los sensores de flujo y presión se encuentran instalados correctamente.
Curso Básico de Eventos: | 1. Recibe instrucción de inicio de lectura 2. Realiza la lectura del sensor de flujo 3. Realiza la lectura del sensor de presión 4. Almacena la información 5. Repite pasos 2 y 3 dependiendo del número de sensores conectados. 6. Conforma un paquete de datos con la información de las lecturas de datos.
Excepciones: | Error de medición en los sensores de flujo y presión
Supuestos: | Se asume que el módulo de proceso conoce el número de sensores flujo y presión conectados a cada nodo actuador.
Postcondiciones: | El módulo de proceso tiene disponible los valores de flujo y presión actuales del área de riego.

# 5. Especificaciones operativas por dispositivo

## 5.1 Nodo Sensor

Requerimiento | R.OPE.01
Nombre | Medición del Nodo Sensor
Operación | Medición del contenido volumétrico de agua en la tierra de cultivo, a tres niveles de profundidad
Variables | Contenido volumétrico de agua, 0% a 100%
Entrada | Mensaje del nodo controlador al nodo sensor para iniciar medición
Salida | Mensaje del nodo sensor al nodo controlador para enviar resultados de la medición
Frecuencia | Periódico, cada minuto

## 5.2 Nodo Climático

Requerimiento | R.OPE.02
Nombre | Medición del Nodo Climático
Operación | Medición de variables ambientales como humedad relativa, temperatura del aire, presión atmosférica, velocidad del viento y radiación solar. Cálculo de la evapotranspiración de referencia por medio de la fórmula Penman-Monteith FAO 56
Variables | Humedad relativa, 0% a 100% Temperatura del aire, oC Velocidad del viento, m/s Radiación solar, W/m² Evapotranspiración de referencia, mm/día
Entrada | Mensaje del nodo controlador al nodo climático para iniciar medición
Salida | Mensaje del nodo climático al nodo controlador para enviar resultados de la medición
Frecuencia | Periódico, cada minuto

## 5.3 Nodo Actuador

Requerimiento | R.OPE.03
Nombre | Accionamiento/Medición del Nodo Actuador
Operación | Activación y desactivación el flujo de agua en el sistema de riego mediante el accionamiento de bombas de agua y/o válvulas de flujo. Medición de variables del sistema hidráulico como flujo y presión de agua.
Variables | Flujo de agua, litros por minuto Presión de agua, bars Encendido /apagado de la bomba de agua Encendido/apagado de la válvula de flujo
Entrada | Mensaje del nodo controlador al nodo actuador para realizar el accionamiento y la medición
Salida | Mensaje del nodo actuador al nodo controlador para enviar resultados del accionamiento y la medición
Frecuencia | Periódico, cada minuto

## 5.4 Nodo Repetidor

Requerimiento | R.OPE.04
Nombre | Retransmisión del Nodo Repetidor
Operación | Retransmitir un mensaje proveniente del nodo controlador un nodo fuera de alcance (nodos sensores, actuadores o climáticos ).
Variables | Ninguna
Entrada | Mensaje del nodo controlador al nodo repetidor.
Salida | Mensaje del nodo repetidor al nodo fuera de alcance.
Frecuencia | Periódico, cada minuto

## 5.5 Nodo Controlador

Requerimiento | R.OPE.05
Nombre | Lectura de humedad de suelo
Operación | Recepción de datos de contenido volumétrico de agua en la tierra de cultivo, proveniente del nodo sensor
Variables | Contenido volumétrico de agua, 0% a 100%
Entrada | Mensaje del nodo controlador al nodo sensor.
Salida | Mensaje del nodo sensor al nodo controlador con los datos de la medición.
Frecuencia | Periódico, cada minuto

Requerimiento | R.OPE.06
Nombre | Lectura de variables climáticas
Operación | Recepción de variables ambientales como humedad relativa, temperatura del aire, presión atmosférica, velocidad del viento y radiación solar.
Variables | Humedad relativa, 0% a 100% Temperatura del aire, oC Velocidad del viento, m/s Radiación solar, W/m² Evapotranspiración de referencia, mm/day
Entrada | Mensaje del nodo controlador al nodo climático para la lectura
Salida | Mensaje del nodo climático al nodo controlador con los datos de la medición.
Frecuencia | Periódico, cada minuto

Requerimiento | R.OPE.07
Nombre | Cálculo de error actual
Operación | Calcular el error actual de humedad de suelo, a partir de la lectura de humedad actual y el valor de referencia deseado.
Variables | Error, de 0% a 100%
Entrada | Lectura de humedad de suelo. Valor de referencia deseado
Salida | Error actual del proceso
Frecuencia | Periódico, cada minuto

Requerimiento | R.OPE.08
Nombre | Algoritmo de control
Operación | Calcular la señal de control adecuada de acuerdo a la necesidad de riego del cultivo
Variables | Señal de control, activar o desactivar válvula y/o bomba
Entrada | Error actual del proceso Evapotranspiración de referencia calculada Modelo matemático del proceso Restricciones de operación
Salida | Señal de control
Frecuencia | Periódico, cada minuto

Requerimiento | R.OPE.09
Nombre | Envío de señal de control
Operación | Enviar la señal de control obtenida por la ejecución del algoritmo de control.
Variables | Encendido /apagado de la bomba de agua Encendido/apagado de la válvula de flujo
Entrada | Mensaje del nodo controlador al nodo actuador para realizar el accionamiento y la medición
Salida | Mensaje del nodo actuador al nodo controlador para enviar resultados del accionamiento y la medición.
Frecuencia | Periódico, cada minuto

Requerimiento | R.OPE.10
Nombre | Transmisión remota
Operación | Enviar actualización de información en forma remota del nodo controlador al servidor de datos.
Variables | Contenido volumétrico de agua, 0% a 100% Humedad relativa, 0% a 100% Temperatura del aire, oC Presión atmosférica, kPa Velocidad del viento, m/s Radiación solar, W/m² Flujo de agua, litros por segundo Presión de agua, bars Encendido /apagado de la bomba de agua Encendido/apagado de la válvula de flujo Evapotranspiración de referencia mm/día
Entrada | Mensaje del nodo controlador al servidor de datos
Salida | Confirmación del servidor de datos al nodo controlador.
Frecuencia | Periódico, cada 10 minutos

Requerimiento | R.OPE.11
Nombre | Configuración del nodo controlador
Operación | El servidor de datos envía al nodo controlador los parámetros relativos a la configuración operativa del controlador
Variables | Modo de operación (Manual, temporizado, automático) Valor de referencia de humedad de suelo, 0% a 100% Modelo matemático del proceso
Entrada | Mensaje del servidor de datos al nodo controlador
Salida | Confirmación del nodo controlador al nodo sensor.
Frecuencia | Esporádico

## 5.6 Servidor de datos

Requerimiento | R.OPE.12
Nombre | Recepción remota
Operación | Recepción de información en forma remota del nodo controlador al servidor de datos.
Variables | Contenido volumétrico de agua, 0% a 100% Humedad relativa, 0% a 100% Temperatura del aire, oC Presión atmosférica, kPa Velocidad del viento, m/s Radiación solar, W/m² Flujo de agua, litros por segundo Presión de agua, bars Encendido /apagado de la bomba de agua Encendido/apagado de la válvula de flujo Evapotranspiración de referencia mm/día
Entrada | Mensaje del nodo controlador al servidor de datos
Salida | Confirmación del servidor de datos al nodo controlador.
Frecuencia | Periódico, cada 10 minutos

Requerimiento | R.OPE.13
Nombre | Configuración de los controladores
Operación | El servidor de datos envía al nodo controlador los parámetros relativos a la configuración operativa del controlador
Variables | Modo de operación (Manual, temporizado, automático) Valor de referencia de humedad de suelo, 0% a 100% Modelo matemático del proceso
Entrada | Mensaje del servidor de datos al nodo controlador
Salida | Confirmación del nodo controlador al nodo sensor.
Frecuencia | Esporádico

Requerimiento | R.OPE.14
Nombre | Almacenamiento en base de datos
Operación | El servidor de datos almacena la información proveniente de los nodos controladores
Variables | Contenido volumétrico de agua, 0% a 100% Humedad relativa, 0% a 100% Temperatura del aire, oC Presión atmosférica, kPa Velocidad del viento, m/s Radiación solar, W/m² Flujo de agua, litros por segundo Presión de agua, bars Encendido /apagado de la bomba de agua Encendido/apagado de la válvula de flujo Evapotranspiración de referencia mm/día
Entrada | Recepción de datos del nodo controlador
Salida | Actualización de la base de datos
Frecuencia | Periódico, cada 10 minutos

Requerimiento | R.OPE.15
Nombre | Configuración del sistema
Operación | El servidor de datos almacena la información proveniente de las aplicaciones de los usuarios
Variables | Modo de operación (Manual, temporizado, automático) Valor de referencia de humedad de suelo, 0% a 100% Modelo matemático del proceso
Entrada | Mensaje de las aplicaciones de usuarios al servidor de datos
Salida | Actualización de la base de datos
Frecuencia | Esporádico

## 5.7 Aplicaciones del Usuario

Requerimiento | R.OPE.16
Nombre | Captura de datos
Operación | El usuario introduce o actualiza los parámetros de operación del sistema
Variables | Modo de operación (Manual, temporizado, automático)
Entrada | Captura de información
Salida | Actualización de la base de datos del servidor
Frecuencia | Esporádico

Requerimiento | R.OPE.17
Nombre | Monitoreo y supervisión
Operación | El usuario supervisa los parámetros críticos del sistema
Variables | Fallas de operación Fallas de comunicación
Entrada | Ninguna
Salida | Ninguna
Frecuencia | Esporádico

Requerimiento | R.OPE.18
Nombre | Desempeño del sistema
Operación | El usuario observa el desempeño del sistema
Variables | Contenido volumétrico de agua, 0% a 100% Humedad relativa, 0% a 100% Temperatura del aire, oC Presión atmosférica, kPa Velocidad del viento, m/s Radiación solar, W/m² Flujo de agua, litros por segundo Presión de agua, bars Encendido /apagado de la bomba de agua Encendido/apagado de la válvula de flujo Evapotranspiración de referencia mm/día
Entrada | Selección de área de riego, fechas y parámetros
Salida | Gráficas con la información solicitada
Frecuencia | Esporádico

INFORMACIÓN DE USO INTERNO COPYRIGHT © 2018, INSTITUTO TECNOLÓGICO Y DE ESTUDIOS SUPERIORES DE MONTERREY

Página i of 25 INFORMACIÓN DE USO INTERNO COPYRIGHT © 2018, INSTITUTO TECNOLÓGICO Y DE ESTUDIOS SUPERIORES DE MONTERREY

Especificaciones Funcionales CHIH-2018-C03-194128

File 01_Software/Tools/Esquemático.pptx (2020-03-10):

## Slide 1

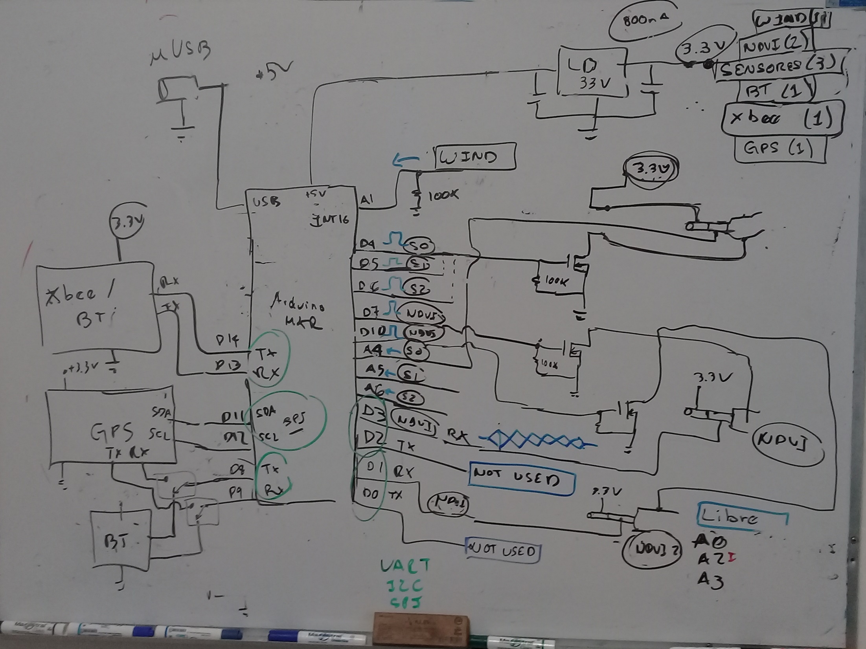
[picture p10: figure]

Bluetooth

GPS

Xbee

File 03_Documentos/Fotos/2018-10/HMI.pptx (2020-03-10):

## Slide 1

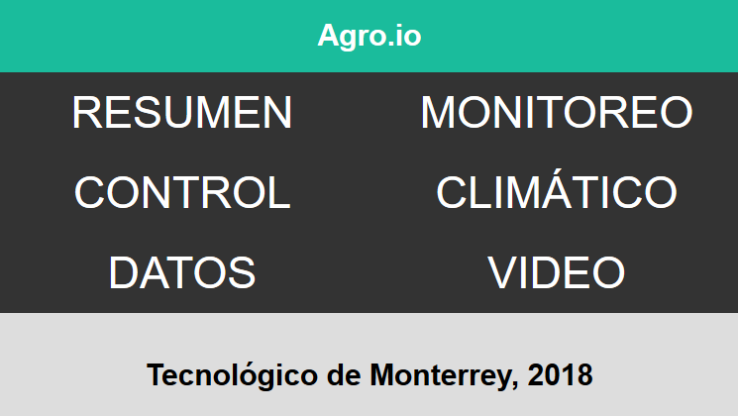
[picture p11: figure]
Screen Clipping

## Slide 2

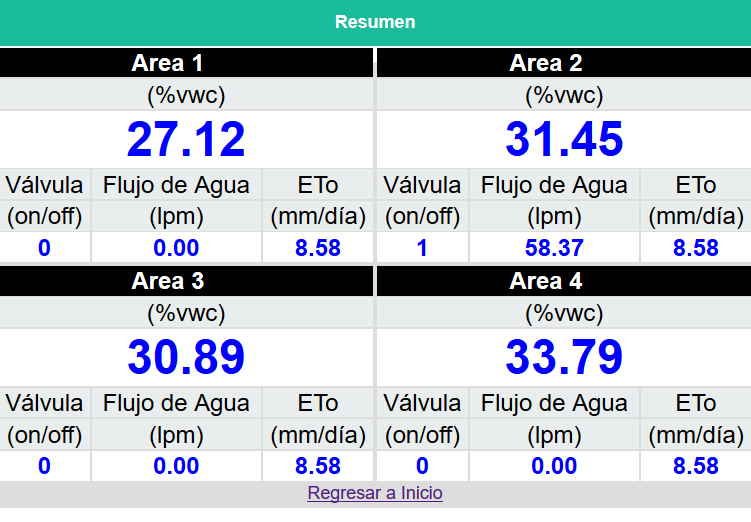
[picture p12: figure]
Screen Clipping

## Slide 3

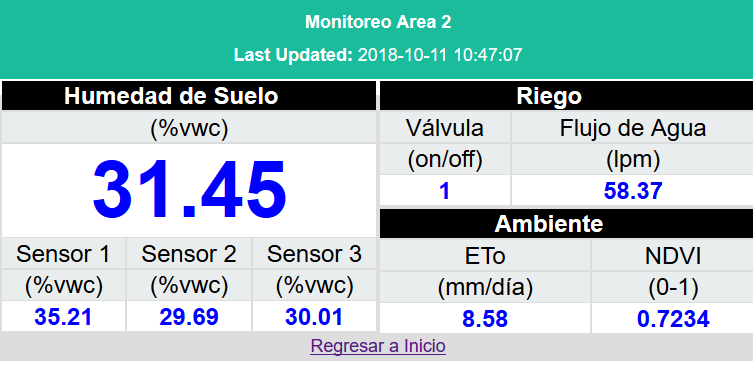
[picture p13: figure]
Screen Clipping

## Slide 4

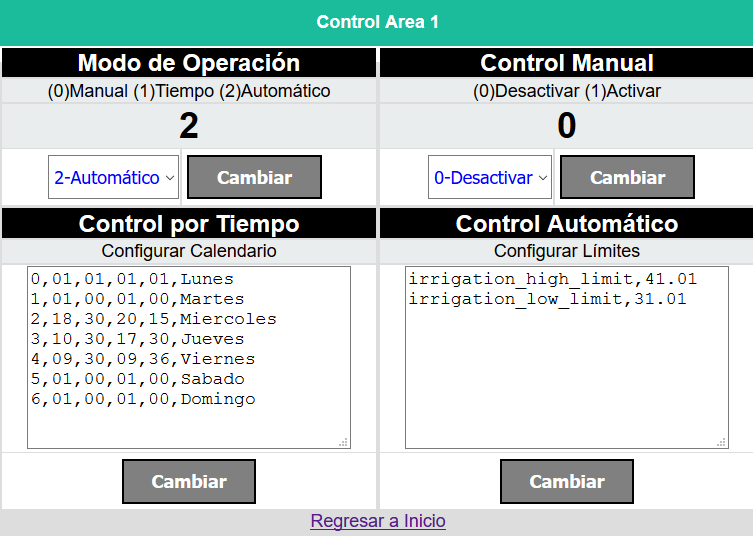
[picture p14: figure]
Screen Clipping

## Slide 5

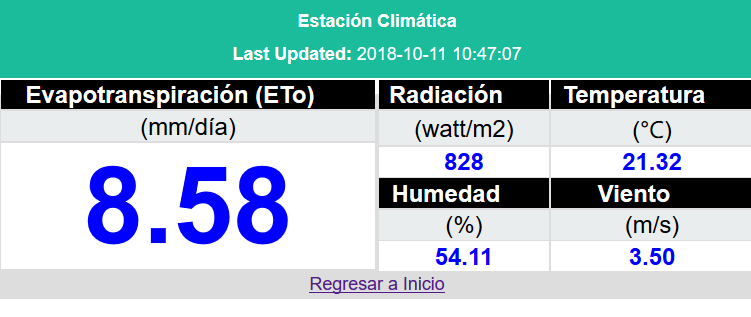
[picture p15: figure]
Screen Clipping

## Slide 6

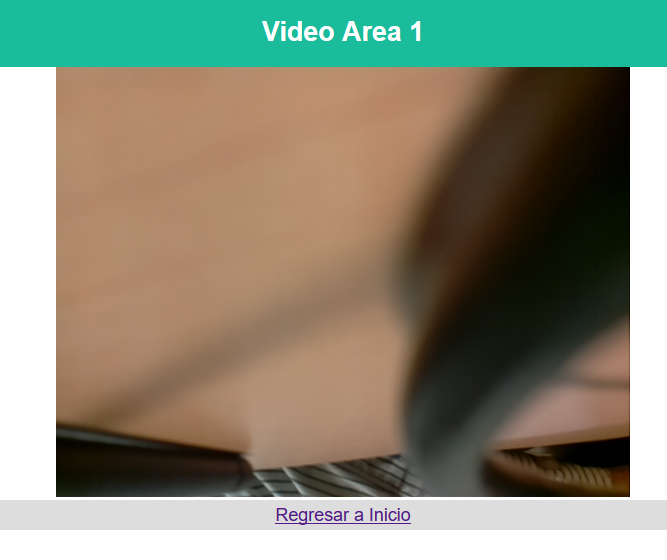
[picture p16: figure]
Screen Clipping
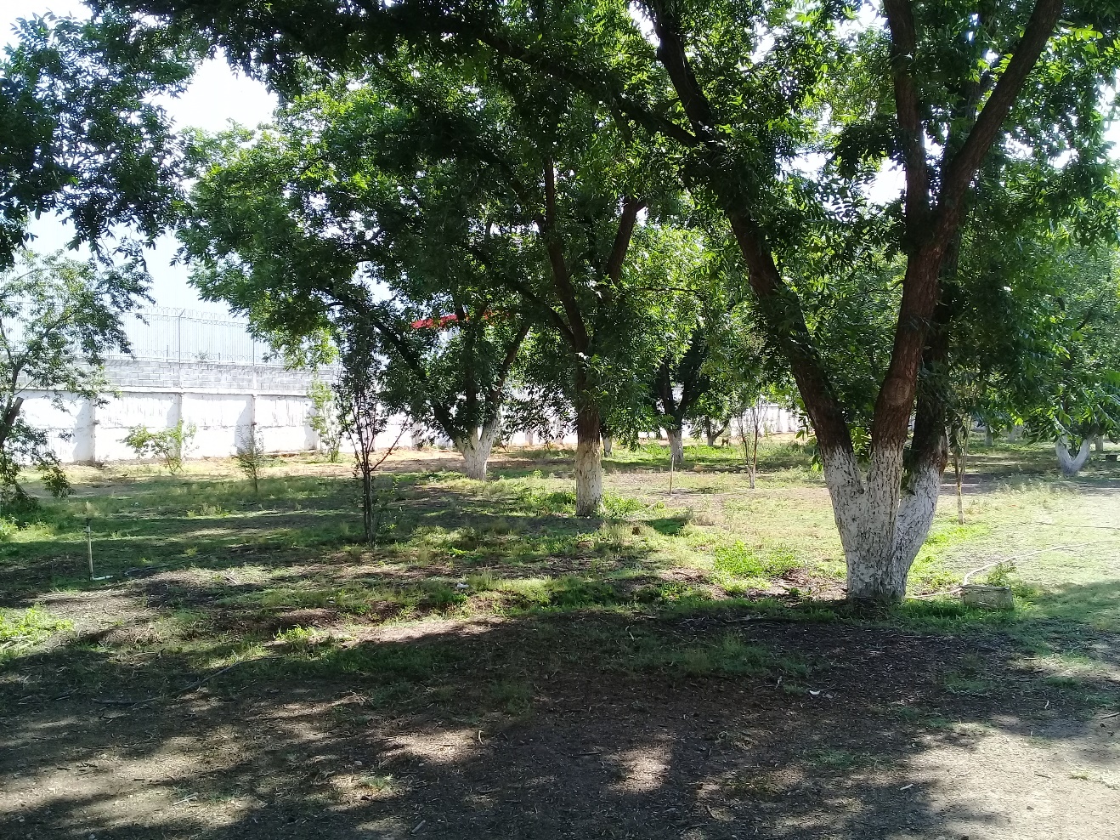
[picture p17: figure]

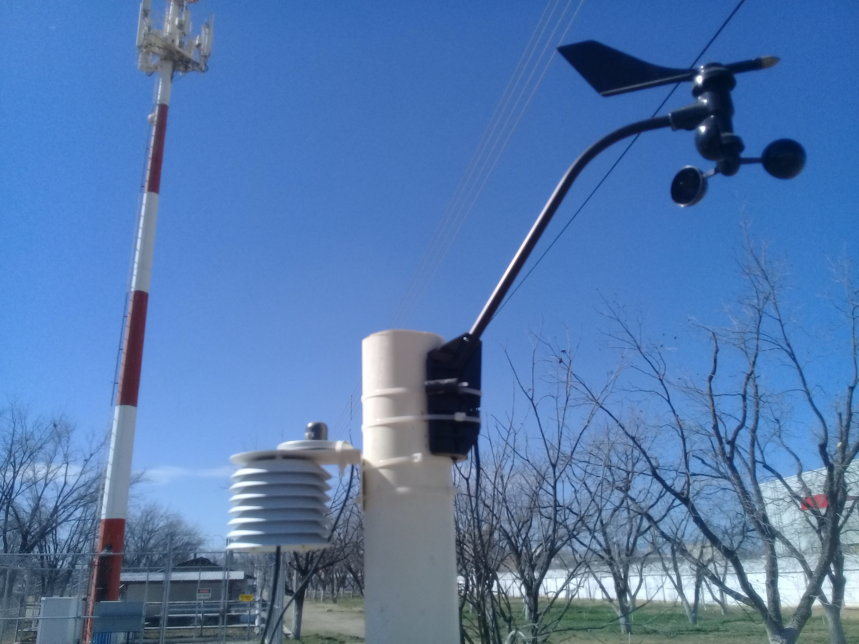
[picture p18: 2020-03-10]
03_Documentos/Fotos/2019-01/20190207_123052 - Copy.jpg

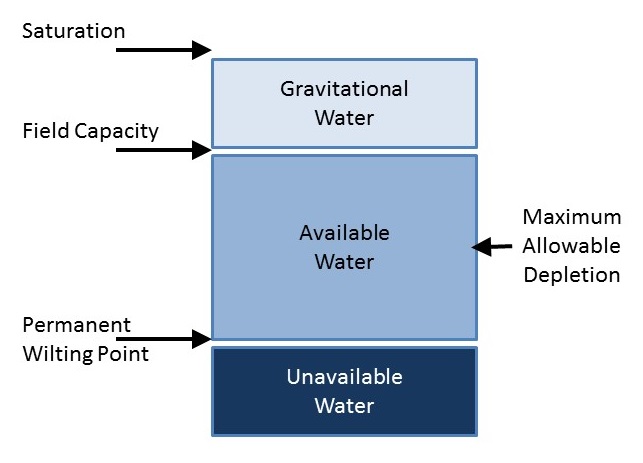
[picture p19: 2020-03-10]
03_Documentos/Fotos/Sistema/Slide3.JPG

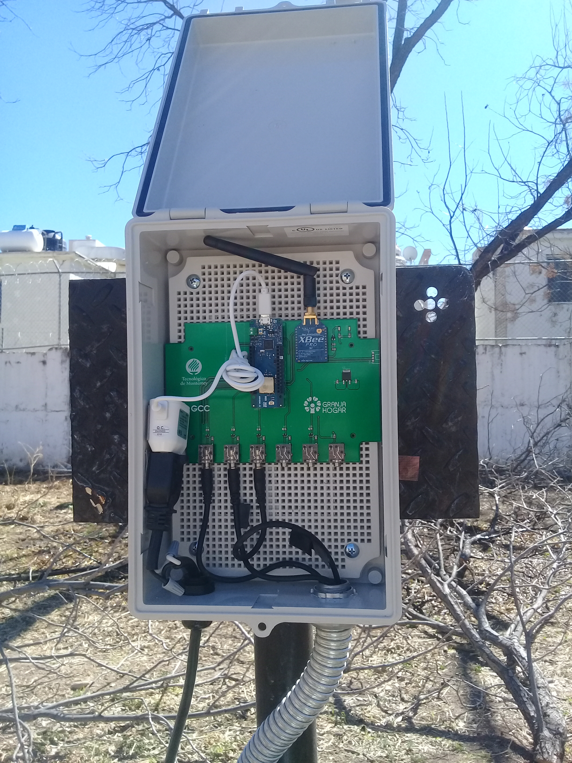
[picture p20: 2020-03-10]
03_Documentos/Fotos/2019-01/20190207_123320 - Copy.jpg

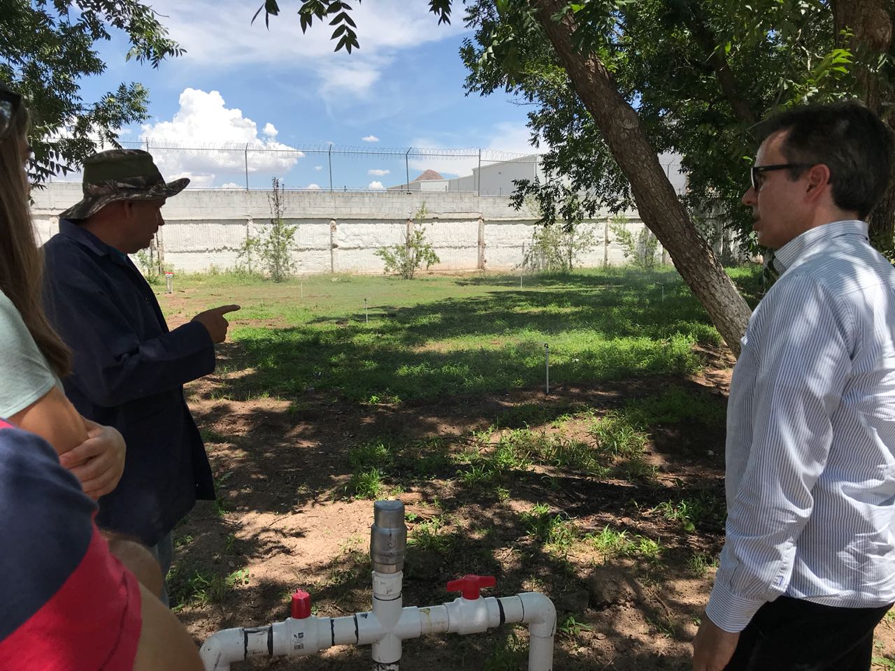
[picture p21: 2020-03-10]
03_Documentos/Fotos/2018-08/IMG-20180811-WA0001.jpg

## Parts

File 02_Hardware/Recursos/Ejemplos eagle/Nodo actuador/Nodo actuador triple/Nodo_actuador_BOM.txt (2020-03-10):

Partlist exported from C:/Users/Carlos/Documents/eagle/Nodo actuador triple/Nodo_actuador_doble.sch at 12/04/2015 02:19:37 p. m.

Part Value             Device            Package       Description                                     MF                      MPN  OC_FARNELL OC_NEWARK PROD_ID 
C1                     C-US050-024X044   C050-024X044  CAPACITOR, American symbol                                                                                
C2                     CPOL-USE2.5-6     E2,5-6        POLARIZED CAPACITOR, American symbol                                                                      
C3                     CPOL-USE2.5-6     E2,5-6        POLARIZED CAPACITOR, American symbol                                                                      
D1   1N4004            1N4004            DO41-10       DIODE                                                                                                     
D2   1N4004            1N4004            DO41-10       DIODE                                                                                                     
D3   1N4004            1N4004            DO41-10       DIODE                                                                                                     
IC1                    78XXS             78XXS         VOLTAGE REGULATOR                                                                                         
IC2  LM358             LM358             DIP08         Jellybean op-amp                                                                                  IC-09172
IC3  4050N             4050N             DIL16         Hex non-inverting BUFFER                                                                                  
K1   G5LE              G5LE              G5LE          RELAY                                                                        unknown    unknown           
K2   G5LE              G5LE              G5LE          RELAY                                                                        unknown    unknown           
K3   G5LE              G5LE              G5LE          RELAY                                                                        unknown    unknown           
LED1                   LED3MM            LED3MM        LED                                                                                                       
LED2                   LED3MM            LED3MM        LED                                                                                                       
LED3                   LED3MM            LED3MM        LED                                                                                                       
OK1  4N35              4N35              DIL06         MOTOROLA OPTO COUPLER                           FAIRCHILD SEMICONDUCTOR 4N35 1328375    72K9946           
OK2  4N35              4N35              DIL06         MOTOROLA OPTO COUPLER                           FAIRCHILD SEMICONDUCTOR 4N35 1328375    72K9946           
OK3  4N35              4N35              DIL06         MOTOROLA OPTO COUPLER                           FAIRCHILD SEMICONDUCTOR 4N35 1328375    72K9946           
R1   330               R-US_0204/7       0204/7        RESISTOR, American symbol                                                                                 
R2                     R-TRIMMT93YA      RTRIMT93YA    Trimm resistor                                                                                            
R3   1k                R-US_0204/7       0204/7        RESISTOR, American symbol                                                                                 
R4   1k                R-US_0204/7       0204/7        RESISTOR, American symbol                                                                                 
R5   1k                R-US_0204/7       0204/7        RESISTOR, American symbol                                                                                 
R6   1k                R-US_0204/7       0204/7        RESISTOR, American symbol                                                                                 
R7   1k                R-US_0204/7       0204/7        RESISTOR, American symbol                                                                                 
R8   1k                R-US_0204/7       0204/7        RESISTOR, American symbol                                                                                 
U$1  ARDUINO_R3_SHIELD ARDUINO_R3_SHIELD UNO_R3_SHIELD Shield form compatible with the Arduino Uno R3.                                                           
U$2  XBEE-1B1          XBEE-1B1          XBEE-1        Xbee module footprints                                                                                    
X1                     AK500/2           AK500/2       CONNECTOR                                                                    unknown    unknown           
X2                     AK500/2           AK500/2       CONNECTOR                                                                    unknown    unknown           
X3                     AK500/2           AK500/2       CONNECTOR                                                                    unknown    unknown           
X4                     AK500/2           AK500/2       CONNECTOR                                                                    unknown    unknown           
X5                     AK500/2           AK500/2       CONNECTOR                                                                    unknown    unknown

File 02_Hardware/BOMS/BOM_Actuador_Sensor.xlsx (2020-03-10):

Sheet: Actuador
BOM: NODO ACTUADOR WA4 V1
Cantidad | Componente | Descripcion | Valor | No. Parte | Fabricante | Link | Costo unitario | Costo total | Aplicación | Notas
1 | CONN_1 | Conector AC C-8 | - | 2570-2210 | Schurter | Mouser (https://www.mouser.mx/ProductDetail/Schurter/43000103) | $0.8840 | $0.884 | Conector de alimentacion principal
1 | T1 | Transformador | 24 V 48VA | FP24-2000 | Triad Magnetics | Mouser (https://www.mouser.mx/ProductDetail/Triad-Magnetics/FP24-2000) | $22.9700 | $22.970 | Fuente de alimentacion principal
1 | B1 | Puente rectificador | 4A | GBU4J | ON Semiconductor | Mouser (https://www.mouser.mx/ProductDetail/ON-Semiconductor-Fairchild/GBU4J?qs=sGAEpiMZZMuQUXCJI7Y4lnFkPbTv3PHy) | $1.5200 | $1.520 | Fuente de alimentacion principal
1 | U1 | Regulador Buck | 500 KHz | TPS54202HDDCR | Texas Instruments | Mouser (https://www.mouser.mx/ProductDetail/Texas-Instruments/TPS54202HDDCR) | $2.1800 | $2.180 | Fuente de 5V
1 | C1 | Capacitor electrolitico | 1000 uF 25V | ECA-1EHG102 | Panasonic | Mouser (https://www.mouser.mx/ProductDetail/Panasonic/ECA-1EHG102?qs=sGAEpiMZZMtZ1n0r9vR22YuzYhk2RkTKiYLI23KOHIo%3d) | $0.9620 | $0.962
2 | C2,C10 | Capacitor ceramico | 10 uF 16V | GRM21BC81C106KA73L | Murata | Mouser (https://www.mouser.mx/ProductDetail/Murata-Electronics/GRM21BC81C106KA73L) | $0.6630 | $1.326
3 | C3,C4,C9 | Capacitor ceramico | 0.1 uF | 08053C104KAT2A | AVX | Mouser (https://www.mouser.mx/ProductDetail/AVX/08053C104KAT2A?qs=sGAEpiMZZMs0AnBnWHyRQO9s69WCSOSMUzR9VHMAygs%3d) | $0.2340 | $0.702
1 | R1 | Resistencia | 510 kΩ | RR1220P-514-D | Susumu | Mouser (https://www.mouser.mx/ProductDetail/Susumu/RR1220P-514-D) | $0.1300 | $0.130
1 | R2 | Resistencia | 51 Ω | RR1220Q-510-D | Susumu | Mouser (https://www.mouser.mx/ProductDetail/Susumu/RR1220Q-510-D) | $0.1300 | $0.130
1 | R3 | Resistencia | 100 kΩ | RR1220P-104-D | Susumu | Mouser (https://www.mouser.mx/ProductDetail/Susumu/RR1220P-104-D?qs=sGAEpiMZZMtlubZbdhIBIHPiT0YkkodQxrHTIurjrno%3d) | $0.1300 | $0.130
1 | R4 | Resistencia | 13.3 kΩ | RR1220P-1332-D-M | Susumu | Mouser (https://www.mouser.mx/ProductDetail/Susumu/RR1220P-1332-D-M?qs=sGAEpiMZZMtlubZbdhIBIHPiT0YkkodQ8PYccqa61Rw%3d) | $0.1430 | $0.143
2 | C5,C6 | Capacitor ceramico | 22 uF 6.3V | GRM219R60J226MEA0D | Murata | Mouser (https://www.mouser.mx/ProductDetail/Murata-Electronics/GRM219R60J226MEA0D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) | $0.4680 | $0.936
1 | C7 | Capacitor ceramico | 75 pF | 08051A750JAT2A | AVX | Mouser (https://www.mouser.mx/ProductDetail/AVX/08051A750JAT2A?qs=sGAEpiMZZMs0AnBnWHyRQKZcV7shucx06N7wLweJMnM%3d) | $0.3770 | $0.377
1 | L1 | Inductor | 15 uH | VLS5045EX-150M-CA | TDK | Mouser (https://www.mouser.mx/ProductDetail/TDK/VLS5045EX-150M-CA) | $0.7540 | $0.754
1 | C8 | Capacitor ceramico | 0.33 uF | 885012207048 | Wurth Electronics | Mouser (https://www.mouser.mx/ProductDetail/Wurth-Electronics/885012207048) | $0.1430 | $0.143
1 | U2 | Regulador lineal | 3.3V | UA78M33IKVURG3 | Texas Instruments | Mouser (https://www.mouser.mx/ProductDetail/Texas-Instruments/UA78M33IKVURG3) | $1.0100 | $1.010 | Fuente de 3.3V
40 | - | Contacto para cable | - | 1-794606-2 | Te Connectivity | Mouser (https://www.mouser.mx/ProductDetail/TE-Connectivity-AMP/1-794606-2-Cut-Strip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) | $0.1010 | $4.040 | Contactos para cables de botones, LEDs, sensores de flujo y valvulas
1 |  | Conector hembra 16 pin | 16 pin 2 rows | 4-794619-6 | Te Connectivity | Mouser (https://www.mouser.mx/ProductDetail/TE-Connectivity-AMP/4-794619-6) | $3.1700 | $3.170 | Conector para botones y LEDs
1 | - | Conector macho 16 pin | 16 pin 2 rows | 1-794617-6 | Te Connectivity | Mouser (https://www.mouser.mx/ProductDetail/TE-Connectivity-AMP/1-794617-6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) | $1.1400 | $1.140 | Conector para botones y LEDs
11 |  | Conector hembra 2 pin | 2 pin 2 rows | 3-794618-2 | Te Connectivity | Mouser (https://www.mouser.mx/ProductDetail/TE-Connectivity-AMP/3-794618-2) | $1.0000 | $11.000 | Conectores para valvulas y sensores
11 | - | Conector macho 2 pin | 2 pin 2 rows | 794617-2 | Te Connectivity | Mouser (https://www.mouser.mx/ProductDetail/TE-Connectivity-AMP/794617-2) | $0.6630 | $7.293 | Conectores para valvulas y sensores
1 | IC1 | Puertas lógicas 2-6V Quad OR | - | MC74HC32ADR2G | ON Semiconductor | Mouser (https://www.mouser.mx/ProductDetail/ON-Semiconductor/MC74HC32ADR2G) | $0.5590 | $0.559 | Para control de valvulas por boton o por software
4 | U3-U6 | Controlador push button | - | MAX16054AZT+T | Maxim Integrated | Mouser (https://www.mouser.mx/ProductDetail/Maxim-Integrated/MAX16054AZT%2bT) | $3.3700 | $13.480 | Eliminación de rebote y proteccion ESD
17 | R5-R11,R17-R20,R22,R24,R26,R28,R35,R37 | Resistencia | 10 kΩ | RR1220P-103-D | Susumu | Mouser (https://www.mouser.mx/ProductDetail/Susumu/RR1220P-103-D) | $0.1300 | $2.210
6 | K1-K6 | Relevador | 5 VDC | G5V-1-2 DC5 | Omron | Mouser (https://www.mouser.mx/ProductDetail/Omron-Electronics/G5V-1-2-DC5?qs=sGAEpiMZZMvi6wO7nhr1L0OnxXmZ2KP4) | $2.8500 | $17.100 | Relevadores para valvulas y activacion de bomba
3 | IC2,IC7,IC8 | Driver relevador | - | MDC3105DMT1G | ON Semiconductor | Mouser (https://www.mouser.mx/ProductDetail/ON-Semiconductor/MDC3105DMT1G?qs=sGAEpiMZZMtqO%252bWUGLBzeFRgH9%252bX7ByJ) | $0.5720 | $1.716
4 | R13-R16 | Resistencia | 1 kΩ | RR1220P-102-D | Susumu | Mouser (https://www.mouser.mx/ProductDetail/Susumu/RR1220P-102-D) | $0.1300 | $0.520
5 | Q1-Q5 | Transistor BJT NPN | - | BCX70K | ON Semiconductor | Mouser (https://www.mouser.mx/ProductDetail/ON-Semiconductor-Fairchild/BCX70K) | $0.3770 | $1.885 | Encendido de LEDs de los botones
4 | - | Push button con LED | Azul | 481 | Adafruit | Mouser / Adafruit (https://www.mouser.mx/ProductDetail/Adafruit/481) | $6.4400 | $25.760 | Botones para encendido manual de valvulas
2 | JP1 | XBEE Header | 10 pin | 366 | Adafruit | Mouser (https://www.mouser.mx/ProductDetail/Adafruit/366?qs=sGAEpiMZZMtyU1cDF2RqUKfg8pKi7bzlRKysq4eQ2IE%3d) | $1.2400 | $2.480 | Socket Xbee
1 | R29 | Potenciometro | 50 kΩ | PVG5A503C03B00 | Bourns | Mouser (https://www.mouser.mx/ProductDetail/Bourns/PVG5A503C03B00?qs=sGAEpiMZZMvygUB3GLcD7qR9snKKmVdvPEfXA94QMhI%3d) | $3.3000 | $3.300 | Referencia de voltaje para sensores de flujo
4 | R21,R23,R25,R27 | Resistencia | 5.1 kΩ | RR1220P-512-D | Susumu | Mouser (https://www.mouser.mx/ProductDetail/Susumu/RR1220P-512-D) | $0.1300 | $0.520
3 | IC3,IC4,IC5 | Amplificador operacional | - | LM358ADR | Texas Instruments | Mouser (https://www.mouser.mx/ProductDetail/Texas-Instruments/LM358ADR?qs=sGAEpiMZZMtYFXwiBRPs0zFXHJUd7gdT) | $0.4680 | $1.404 | Lectura de sensor de flujo
1 | IC6 | Buffer no inversor | - | CD4050BDR | Texas Instruments | Mouser (https://www.mouser.mx/ProductDetail/Texas-Instruments/CD4050BDR) | $0.5460 | $0.546 | Acondicionamiento de señal de sensor de flujo
5 | R30-R34 | Resistencia | 330 Ω 0.5W 0.5% | SG73G2ATTD3300D | KOA | Mouser (https://www.mouser.mx/ProductDetail/KOA-Speer/SG73G2ATTD3300D) | $0.2990 | $1.495
2 | LED1-LED2 | LED | Verde | LTST-C170GKT | Lite On | Mouser (https://www.mouser.mx/ProductDetail/Lite-On/LTST-C170GKT) | $0.3900 | $0.780 | Indicadores
2 | R36,R41 | Resistencia | 330 Ω | RR1220P-331-D | Susumu | Mouser (https://www.mouser.mx/ProductDetail/Susumu/RR1220P-331-D) | $0.1300 | $0.260
1 | U8 | Expansion IO | - | PCF8574DWR | Texas Instruments | Mouser (https://www.mouser.mx/ProductDetail/Texas-Instruments/PCF8574DWR) | $1.9500 | $1.950
2 | - | Header Arduino | 14 pin | M20-7821446 | Harwin | Mouser (https://www.mouser.mx/ProductDetail/Harwin/M20-7821446) | $1.8700 | $3.740
1 | FB1 | Ferrita | - | MPZ2012S102JTD25 | TDK | Mouser (https://www.mouser.mx/ProductDetail/TDK/MPZ2012S102JTD25) | $0.1690 | $0.169
1 | - | Header | 4 pin | M20-7820446 | Harwin | Mouser (https://www.mouser.mx/ProductDetail/Harwin/M20-7820446) | $1.0300 | $1.030
1 | - | Antenna con cable | - | ANT-916-PML-UFL | Linx Technologies | Mouser (https://www.mouser.mx/ProductDetail/Linx-Technologies/ANT-916-PML-UFL) | $12.7400 | $12.740
 |  |  |  |  |  |  | Total | $154.584

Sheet: Actuador PCB
Cantidad | 5

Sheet: Sensor
BOM: NODO SENSOR WA4 V1
Cantidad | Componente | Descripcion | Valor | No. Parte | Fabricante | Link | Costo unitario | Costo total | Aplicación
2 | JP1 | XBEE Header | 10 pin | 366 | Adafruit | Mouser | $1.2400 | $2.480 | Socket Xbee
2 | - | Header Arduino | 14 pin | M20-7821446 | Harwin | Mouser (https://www.mouser.mx/ProductDetail/Harwin/M20-7821446) | $1.8700 | $3.740
1 | - | Header | 4 pin | M20-7820446 | Harwin | Mouser (https://www.mouser.mx/ProductDetail/Harwin/M20-7820446) | $1.0300 | $1.030
1 | U2 | Regulador lineal | 3.3V | UA78M33IKVURG3 | Texas Instruments | Mouser (https://www.mouser.mx/ProductDetail/Texas-Instruments/UA78M33IKVURG3) | $1.0100 | $1.010 | Fuente de 3.3V
7 | C1-C7 | Capacitor ceramico | 0.1 uF | 08053C104KAT2A | AVX | Mouser (https://www.mouser.mx/ProductDetail/AVX/08053C104KAT2A?qs=sGAEpiMZZMs0AnBnWHyRQO9s69WCSOSMUzR9VHMAygs%3d) | $0.2340 | $1.638
2 | LED1-LED2 | LED | Verde | LTST-C170GKT | Lite On | Mouser (https://www.mouser.mx/ProductDetail/Lite-On/LTST-C170GKT) | $0.3900 | $0.780 | Indicadores
5 | Q1-Q4,Q6 | MOSFET N | - | 2N7002L | ON Semiconductor | Mouser (https://www.mouser.mx/ProductDetail/ON-Semiconductor-Fairchild/2N7002L) | $0.2730 | $1.365
1 | Q5 | Transistor BJT NPN | - | BCX70K | ON Semiconductor | Mouser (https://www.mouser.mx/ProductDetail/ON-Semiconductor-Fairchild/BCX70K) | $0.3770 | $0.377 | Encendido de LEDs de los botones
2 | R1,R36 | Resistencia | 330 Ω | RR1220P-331-D | Susumu | Mouser (https://www.mouser.mx/ProductDetail/Susumu/RR1220P-331-D) | $0.1300 | $0.260
8 | R2-R9 | Resistencia | 10 kΩ | RR1220P-103-D | Susumu | Mouser (https://www.mouser.mx/ProductDetail/Susumu/RR1220P-103-D) | $0.1300 | $1.040
6 | X1-X6 | Connector 3.5mm | - | 35RAPC2BH3 | Switchcraft | Mouser (https://www.mouser.mx/ProductDetail/Switchcraft/35RAPC2BH3) | $2.8700 | $17.220
1 | - | Antenna con cable | - | ANT-916-PML-UFL | Linx Technologies | Mouser (https://www.mouser.mx/ProductDetail/Linx-Technologies/ANT-916-PML-UFL) | $12.7400 | $12.740
 |  |  |  |  |  |  | Total | $43.680

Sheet: Sensor PCB
Cantidad | 10

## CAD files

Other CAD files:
02_Hardware/Recursos/Enclosures/pf15-5-10/pf15-5-10.dwg

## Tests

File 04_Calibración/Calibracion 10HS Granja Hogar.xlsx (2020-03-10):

Sample Number | 1 | 2 | 3 | 4 | 5 | 6 |  | Reading | VWC | Reading | VWC
Avg. Percentage | 0% | 10% | 20% | 30% | 40% | 50% |  | 1656 | -1.00 | 667.2527 | -1.0000
Tara (g) | 11.2 | 11.0 | 10.9 | 11.1 | 11.2 | 11.0 |  | 1720 | 8.00 | 693.0403 | 8.0000
Mass of moist soil (g) | 41.6 | 42.3 | 46.6 | 52.2 | 48.0 | 47.6 |  | 2020 | 18.00 | 813.9194 | 18.0000
Mass of dry soil | 41.8 | 40.7 | 43 | 46.1 | 40.5 | 39.3 |  | 2840 | 30.50 | 1144.3223 | 30.5000
Mass (g), volume (cm3) of water | -0.2 | 1.6 | 3.6 | 6.1 | 7.5 | 8.3 |  | 2863 | 37.50 | 1153.5897 | 37.5000
Sample volume (g) | 20 | 20 | 20 | 20 | 20 | 20 |  | 2900 | 41.50 | 1168.4982 | 41.5000
VWC | -1.00 | 8.00 | 18.00 | 30.50 | 37.50 | 41.50
Avg. Reading | 1656 | 1720 | 2020 | 2840 | 2863 | 2900
Analog Voltage (mV) | 667.25 | 693.04 | 813.92 | 1144.32 | 1153.59 | 1168.50
 |  |  |  |  |  |  | 0.0546

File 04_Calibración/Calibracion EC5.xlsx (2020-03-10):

Sample Number | 1 | 2 | 3 | 4 | 5 | 6 | 7
Avg. Percentage | 0% | 10% | 20% | 30% | 40%
Tara [g] | 11.4 | 11.7 | 11.0 | 11.0 | 11.1
Mass of moist soil [g] | 36.6 | 41.9 | 49.4 | 50.5 | 46.9
Mass of dry soil [g] |  |  |  |  |  |  |  | Mediciones por hacer
Mass [g], volume [cm3] of water | 36.6 | 41.9 | 49.4 | 50.5 | 46.9 | 0 | 0
Sample volume | 20 | 20 | 20 | 20 | 20 | 20 | 20
VWC | 183 | 209.5 | 247 | 252.5 | 234.5 | 0 | 0 | Los resultados para la gráfica
Avg. Reading | 2008 | 2494 | 2884 | 3778 | 3898

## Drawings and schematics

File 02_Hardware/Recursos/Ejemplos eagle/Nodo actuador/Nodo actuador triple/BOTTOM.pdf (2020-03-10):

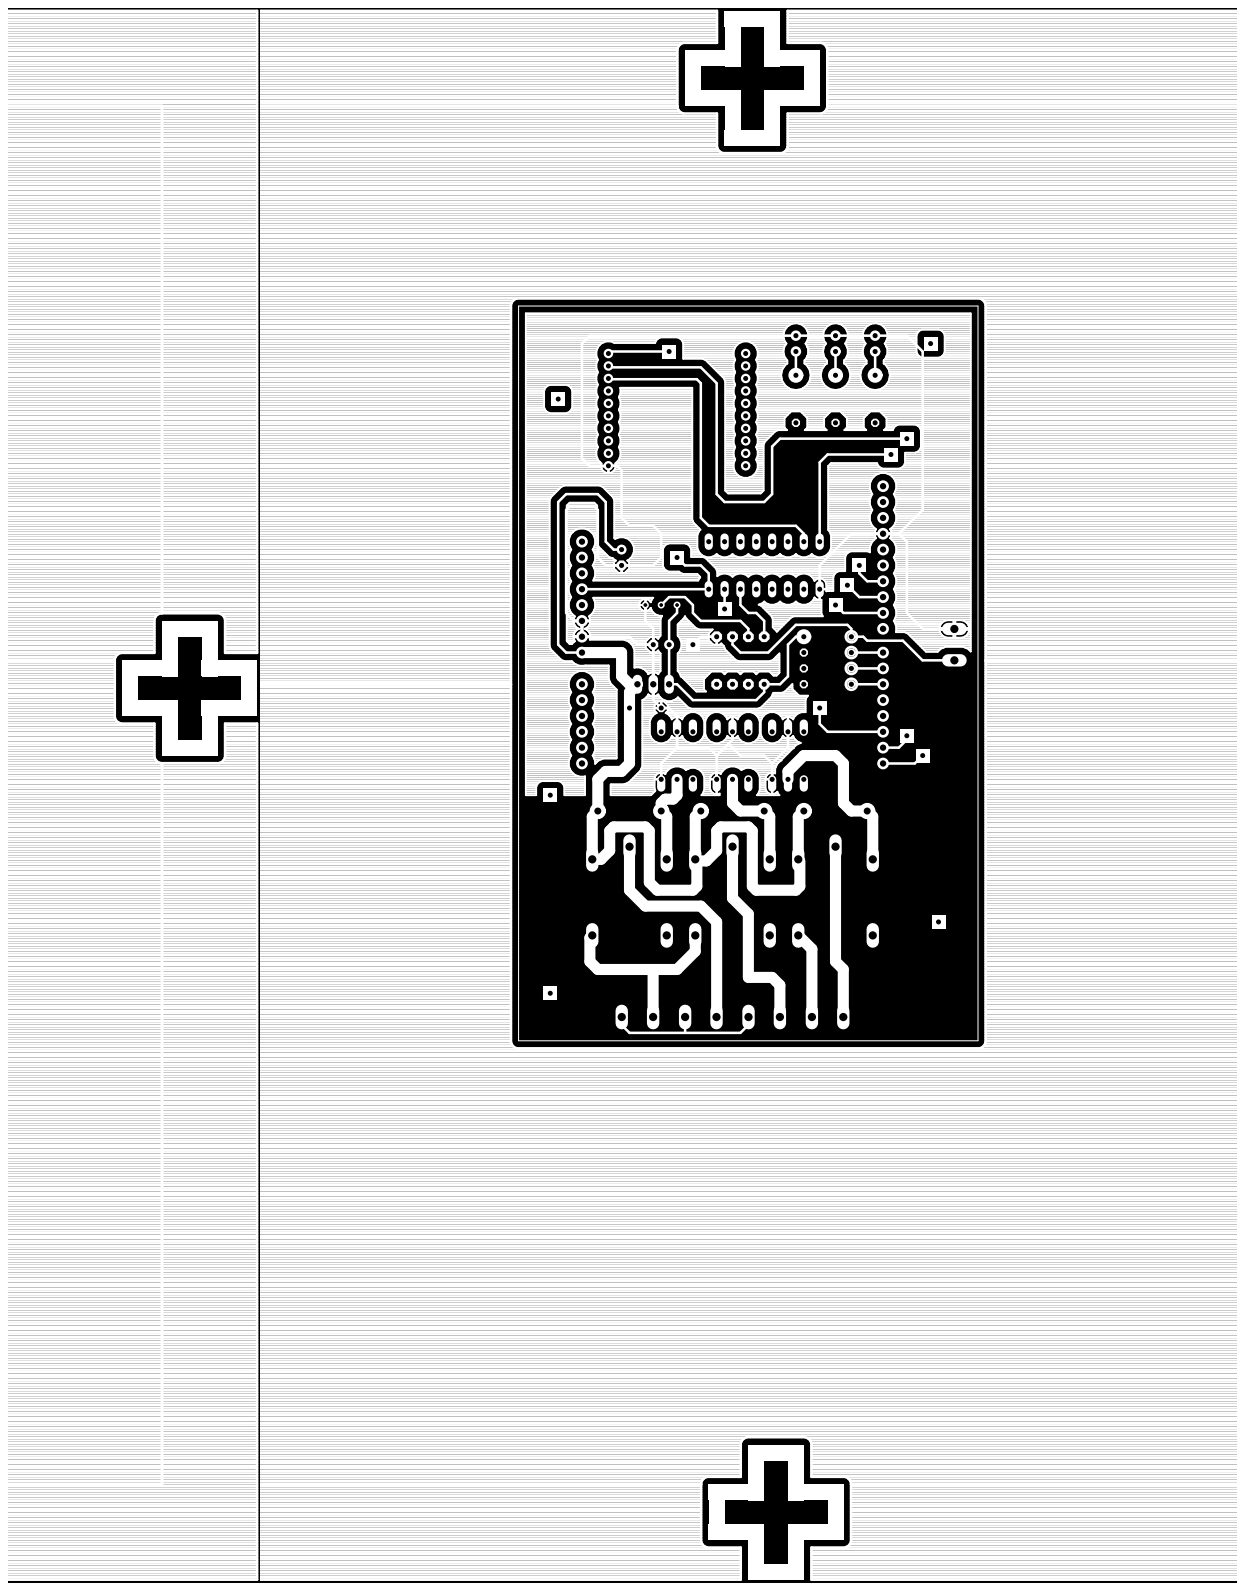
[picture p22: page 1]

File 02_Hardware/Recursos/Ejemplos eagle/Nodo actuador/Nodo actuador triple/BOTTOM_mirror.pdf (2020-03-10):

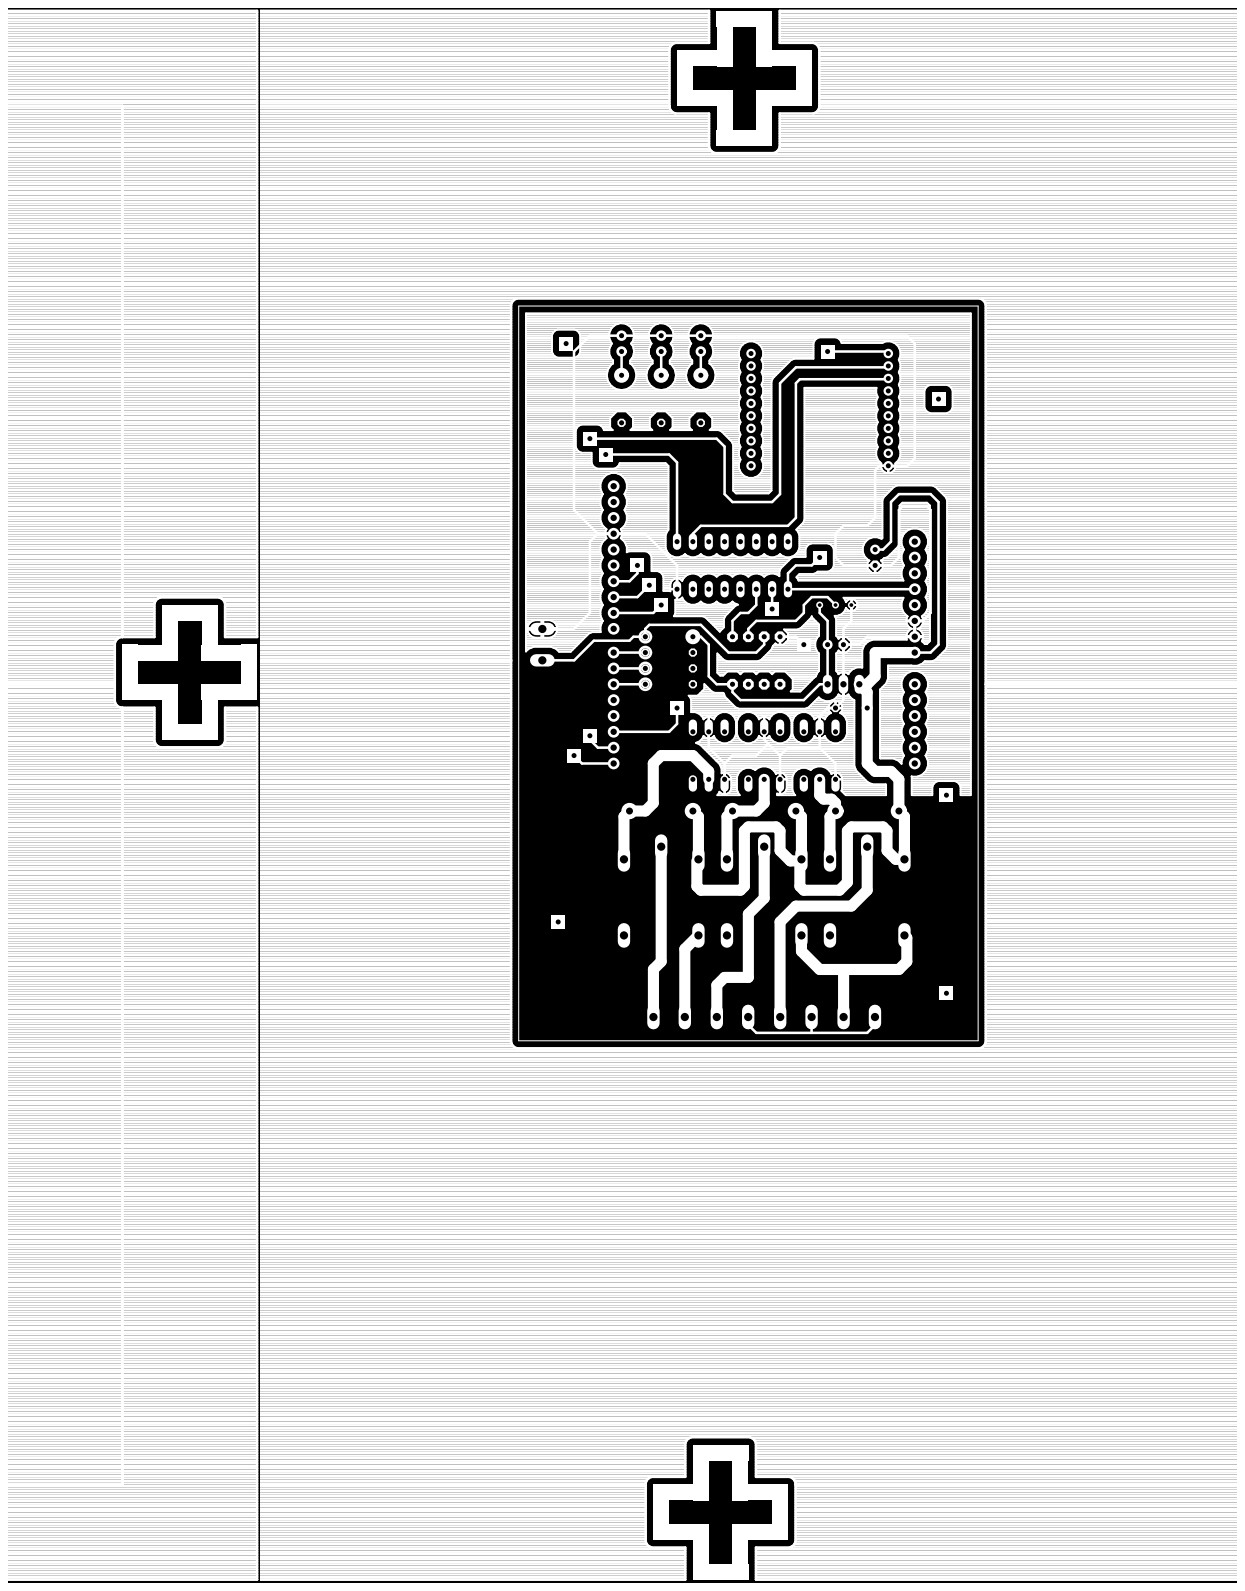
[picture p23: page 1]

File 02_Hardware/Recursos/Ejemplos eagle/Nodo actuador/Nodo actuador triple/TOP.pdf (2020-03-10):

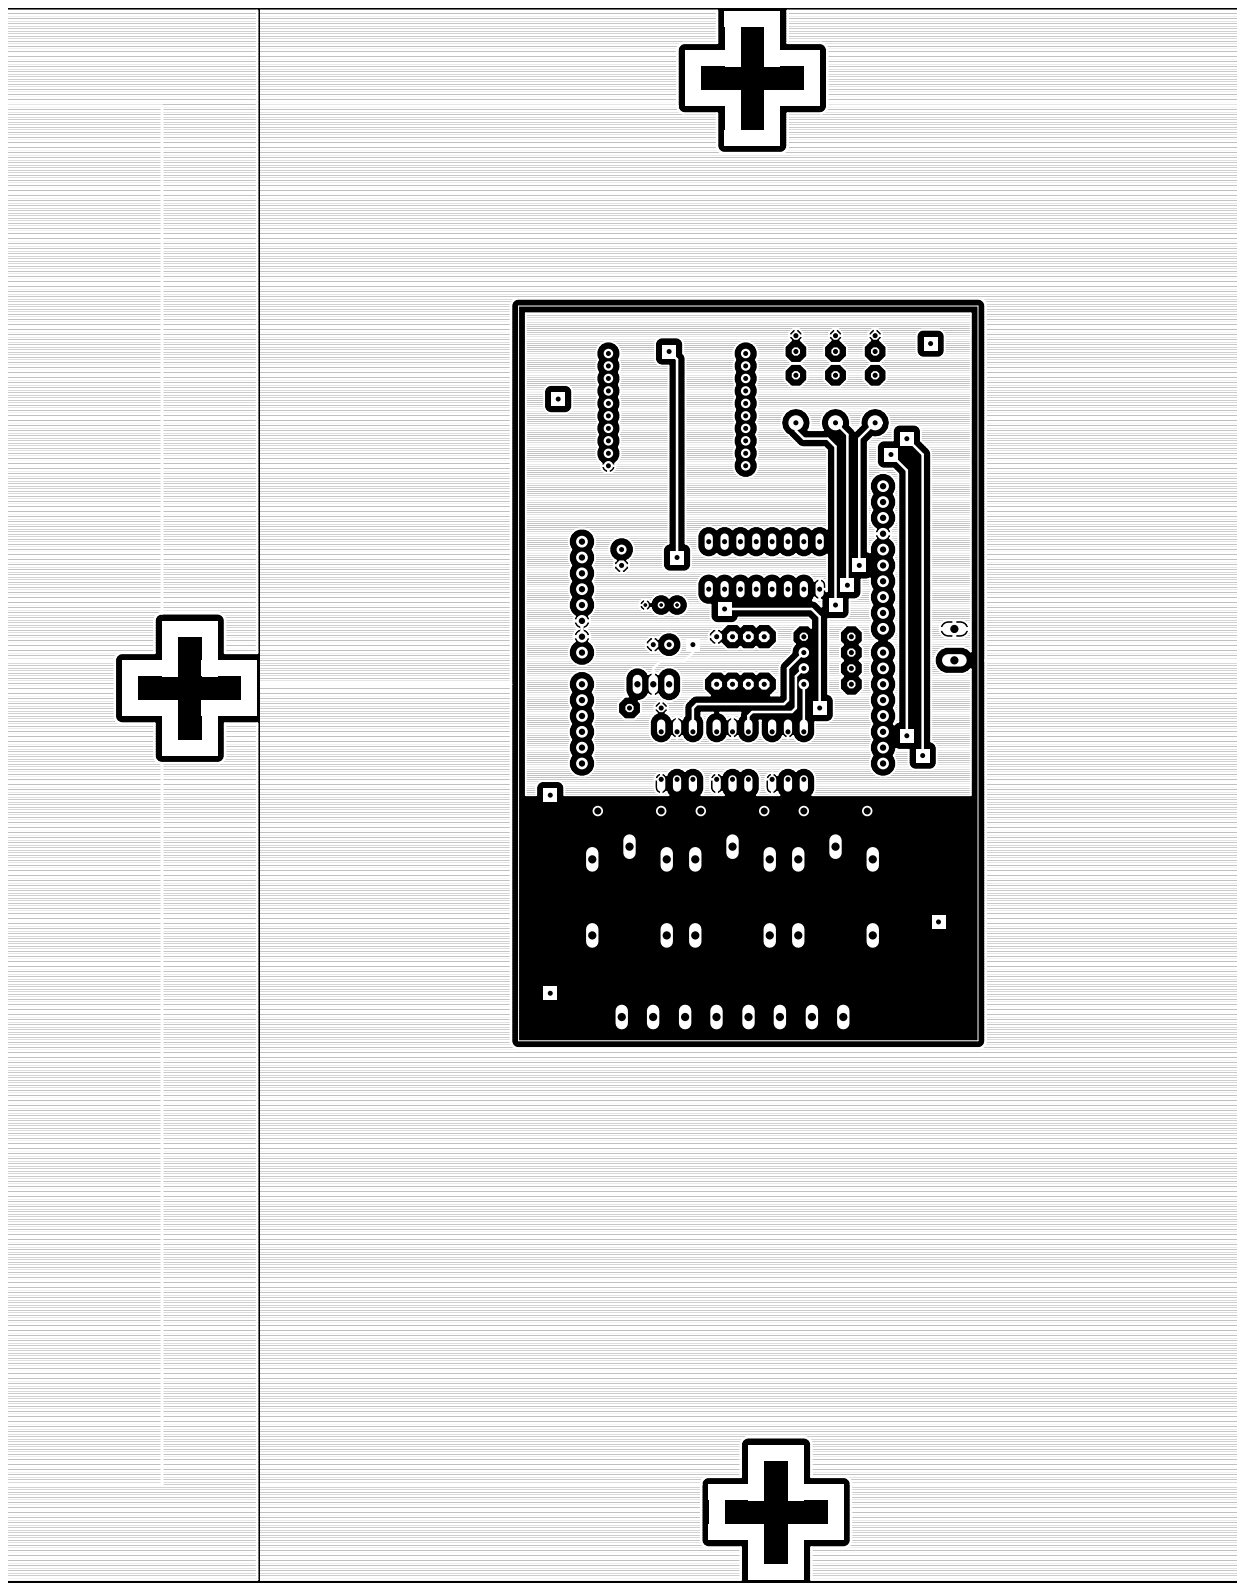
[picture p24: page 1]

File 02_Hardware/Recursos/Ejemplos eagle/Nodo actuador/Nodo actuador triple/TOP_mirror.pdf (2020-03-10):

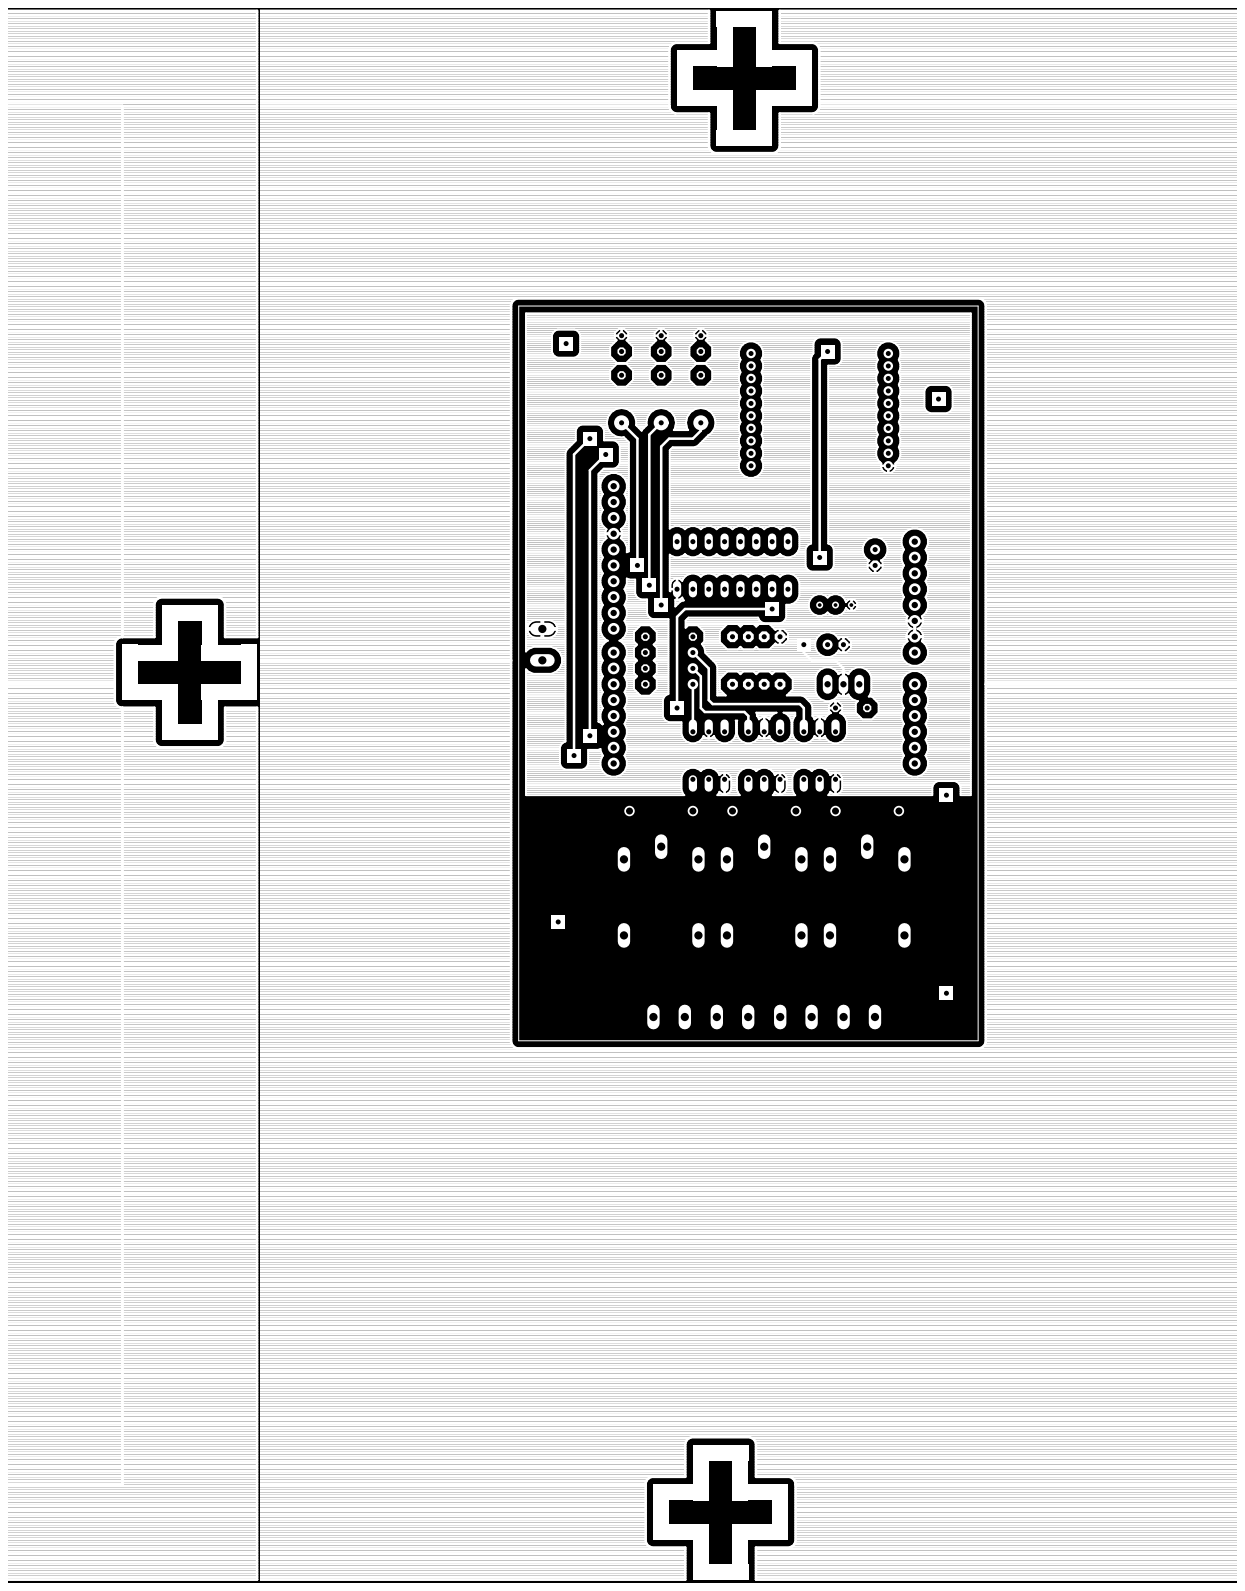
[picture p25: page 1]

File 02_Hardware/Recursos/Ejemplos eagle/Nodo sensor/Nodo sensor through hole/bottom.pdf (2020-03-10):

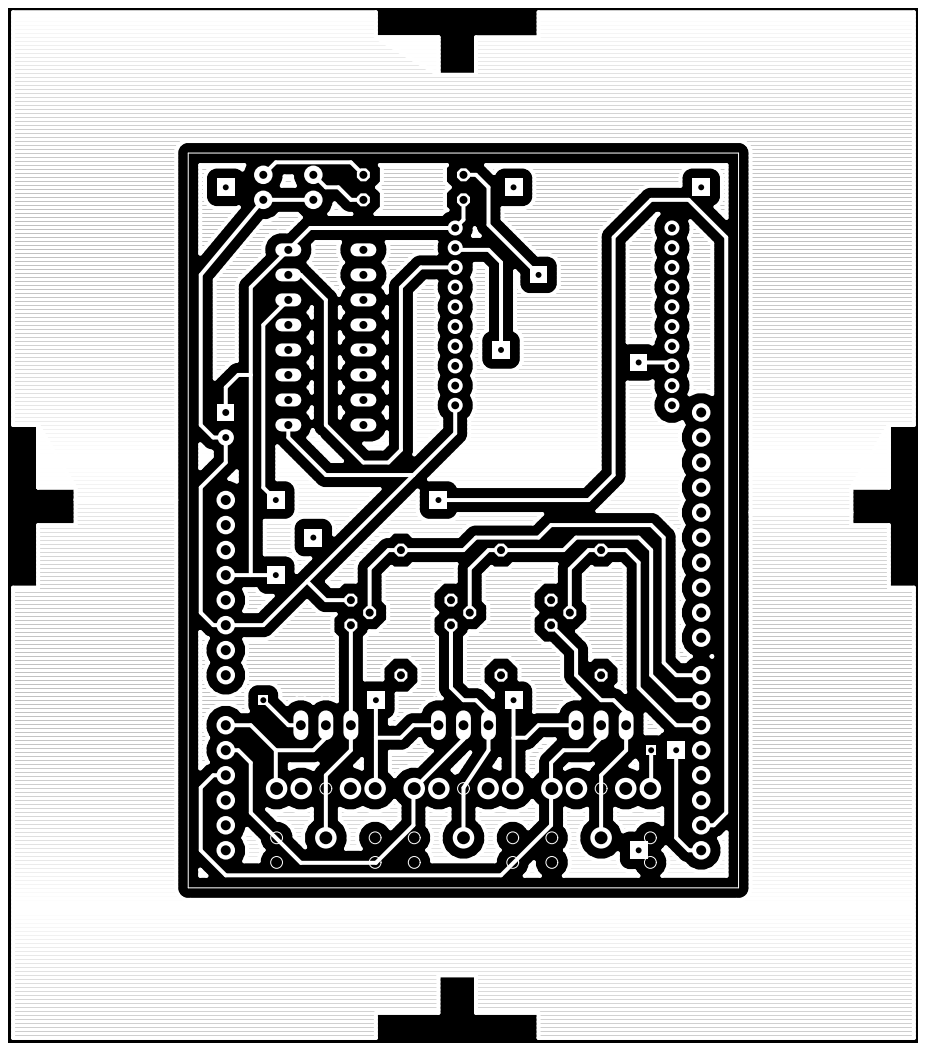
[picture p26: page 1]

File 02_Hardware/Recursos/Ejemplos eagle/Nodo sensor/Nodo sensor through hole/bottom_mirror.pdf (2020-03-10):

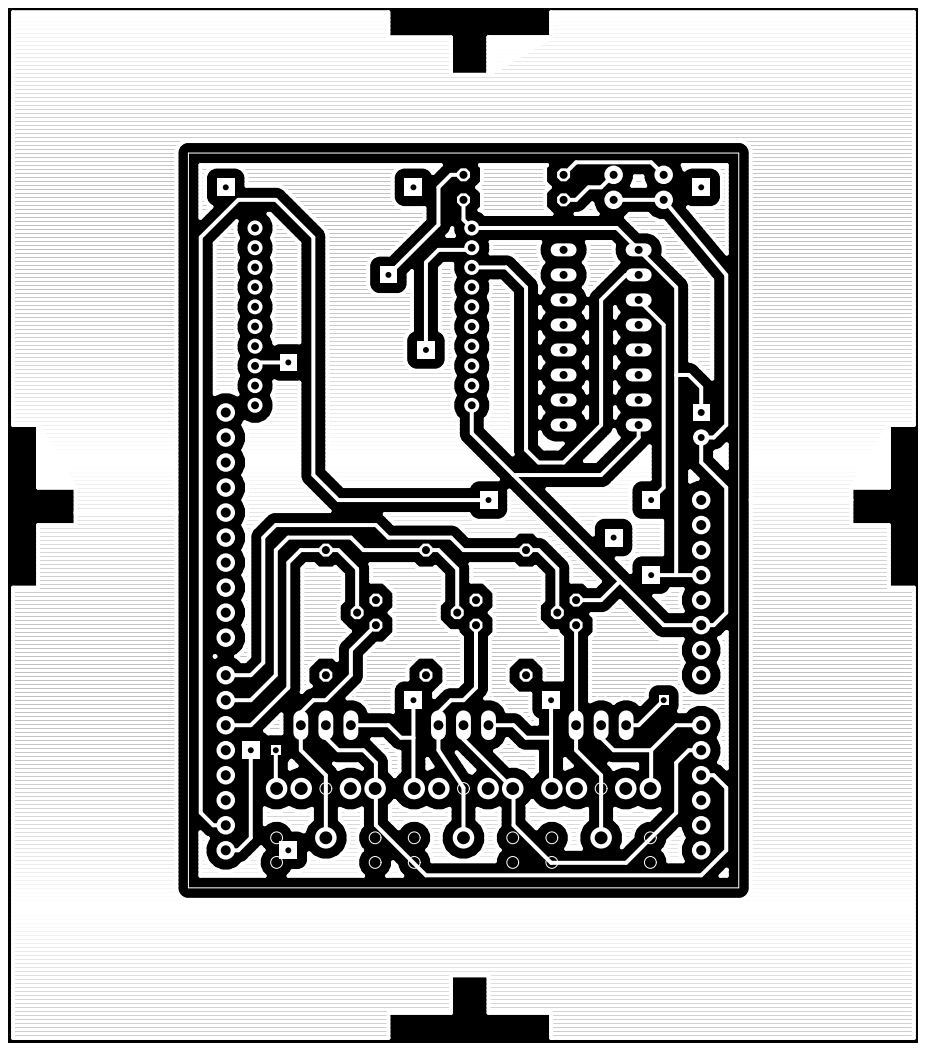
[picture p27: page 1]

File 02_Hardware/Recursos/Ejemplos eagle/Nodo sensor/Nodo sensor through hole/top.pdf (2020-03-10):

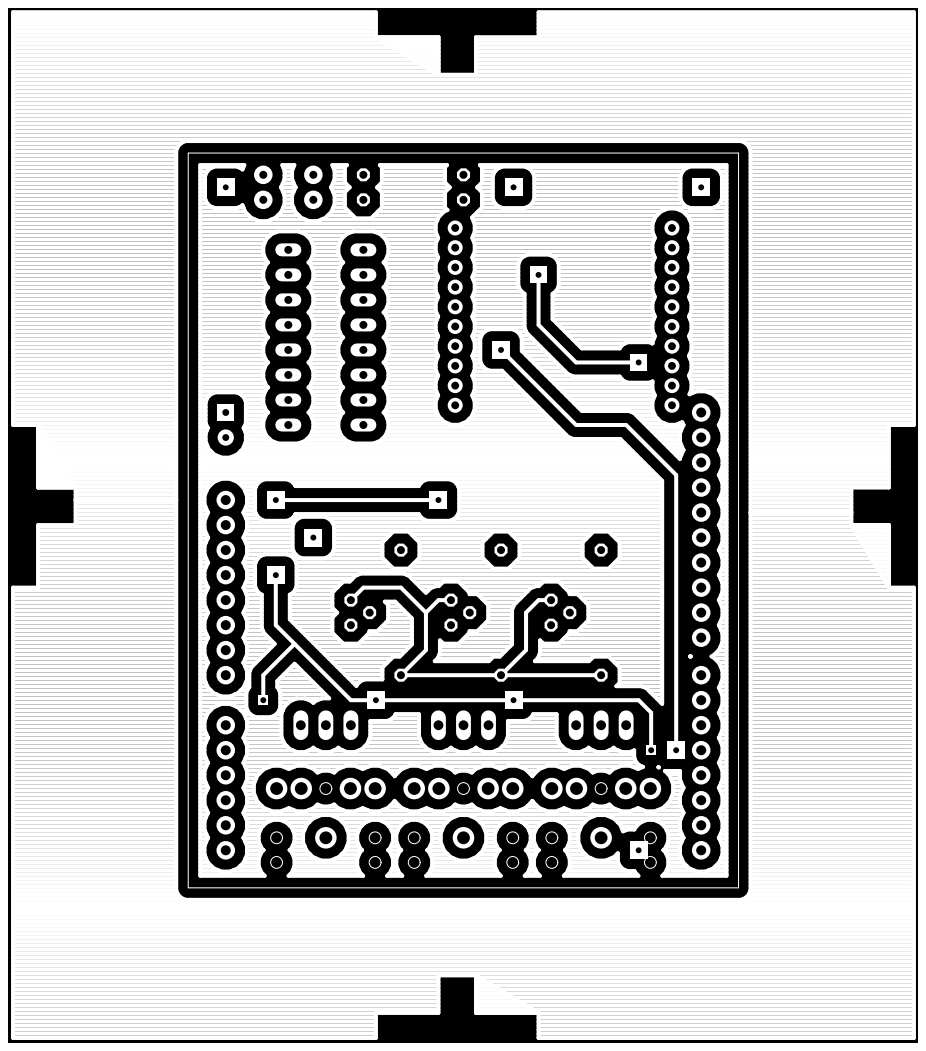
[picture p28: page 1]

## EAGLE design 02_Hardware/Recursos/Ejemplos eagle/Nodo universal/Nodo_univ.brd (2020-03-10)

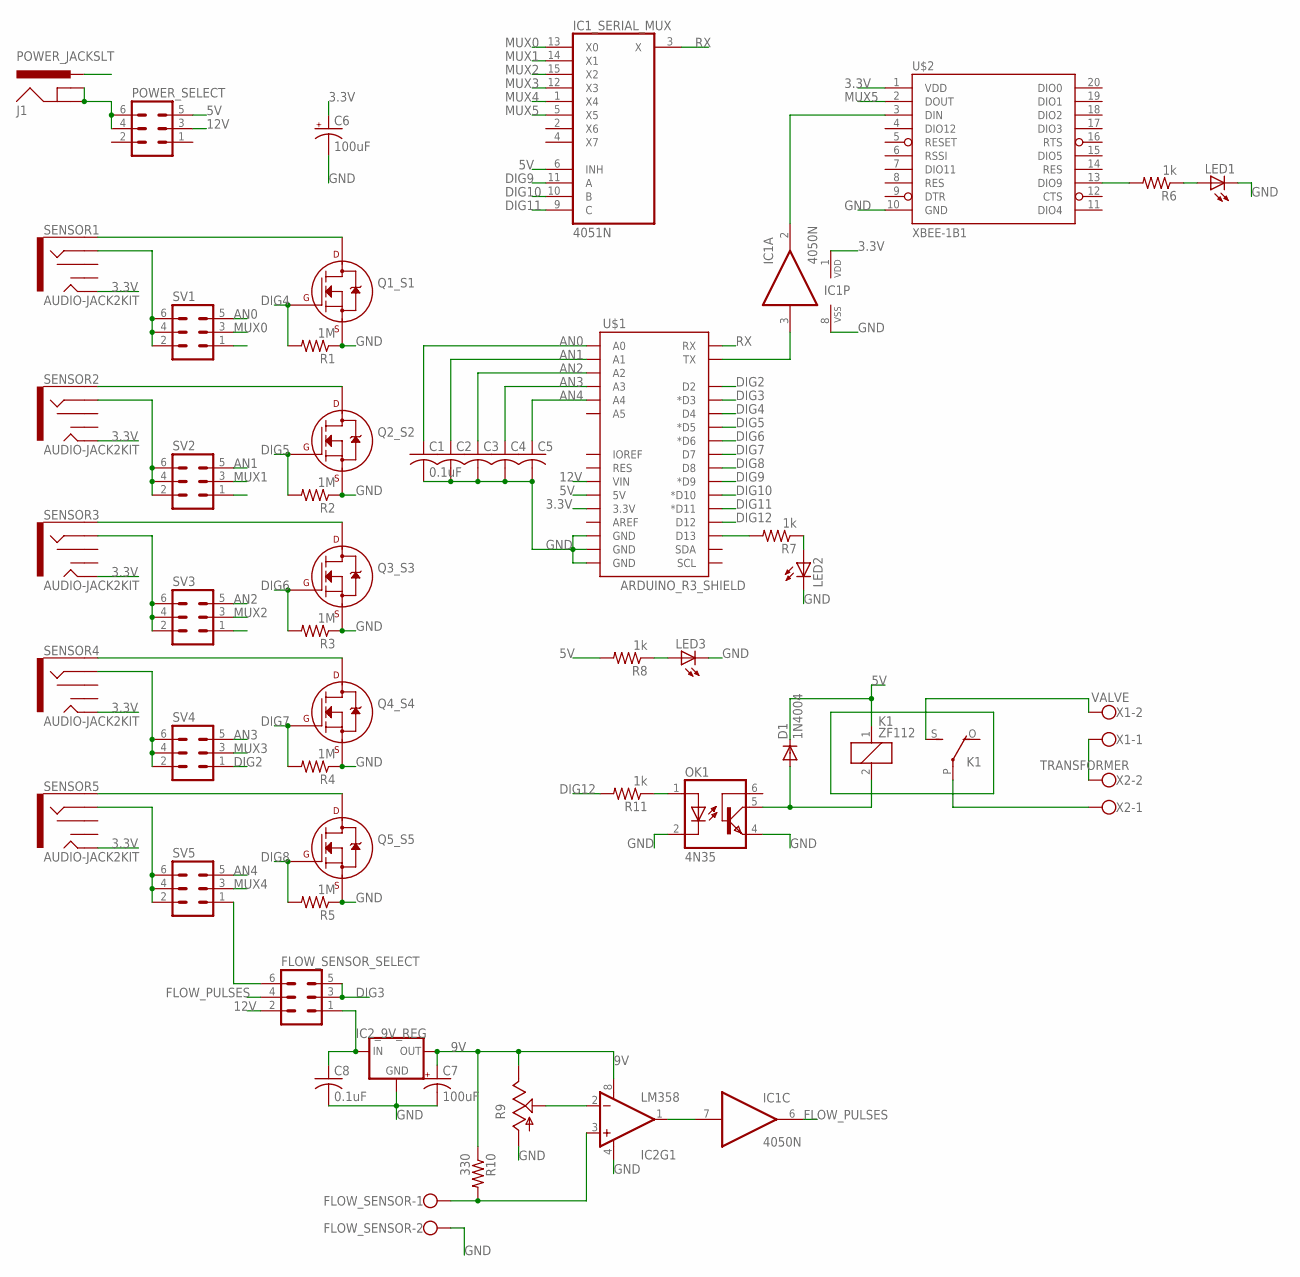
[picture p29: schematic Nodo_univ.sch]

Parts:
C1, C8: 0.1uF; C025-025X050
C2, C3, C4, C5: C-US025-025X050; C025-025X050
C6, C7: 100uF; CPOL-RADIAL-100UF-25V
D1: 1N4004; DO41-10
FLOW_SENSOR: W237-102
FLOW_SENSOR_SELECT: MA03-2
IC1: 4050N; DIL16
IC1_SERIAL_MUX: 4051N; DIL16
IC2: LM358; DIP08
IC2_9V_REG: 78XXL
J1: POWER_JACKSLT; POWER_JACK_SLOT
K1: ZF112
LED1, LED2, LED3: LED3MM
OK1: 4N35; DIL06
POWER_SELECT: MA03-2
Q1_S1, Q2_S2, Q3_S3, Q4_S4, Q5_S5: 2N7000_TO92; TO-92
R1, R2, R3, R4, R5: 1M; 0207/10
R6, R7, R8, R11: 1k; 0207/10
R9: TRIM_US-B64Y; B64Y
R10: 330; 0207/10
SENSOR1, SENSOR2, SENSOR3, SENSOR4, SENSOR5: AUDIO-JACK2KIT; AUDIO-JACK-KIT
SV1, SV2, SV3, SV4, SV5: MA03-2
U$1: ARDUINO_R3_SHIELD; UNO_R3_SHIELD
U$2: XBEE-1B1; XBEE-1
X1: VALVE; W237-102
X2: TRANSFORMER; W237-102

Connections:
3.3V: C6.1 (+), IC1.1 (VDD), SENSOR1.TIP, SENSOR2.TIP, SENSOR3.TIP, SENSOR4.TIP, SENSOR5.TIP, U$1.3.3V, U$2.1 (VDD)
5V: D1.C, IC1_SERIAL_MUX.6 (INH), K1.1, POWER_SELECT.5, R8.2, U$1.5V
9V: C7.1 (+), IC2.8 (V+), IC2_9V_REG.OUT, R9.E, R10.1
12V: FLOW_SENSOR_SELECT.2, POWER_SELECT.3, U$1.VIN
AN0: C1.1, SV1.5, U$1.A0
AN1: C2.1, SV2.5, U$1.A1
AN2: C3.1, SV3.5, U$1.A2
AN3: C4.1, SV4.5, U$1.A3
AN4: C5.1, SV5.5, U$1.A4
DIG2: SV4.1, U$1.D2
DIG3: FLOW_SENSOR_SELECT.3, FLOW_SENSOR_SELECT.5, U$1.D3 (*D3)
DIG4: Q1_S1.2 (G), R1.2, U$1.D4
DIG5: Q2_S2.2 (G), R2.2, U$1.D5 (*D5)
DIG6: Q3_S3.2 (G), R3.2, U$1.D6 (*D6)
DIG7: Q4_S4.2 (G), R4.2, U$1.D7
DIG8: Q5_S5.2 (G), R5.2, U$1.D8
DIG9: IC1_SERIAL_MUX.11 (A), U$1.D9 (*D9)
DIG10: IC1_SERIAL_MUX.10 (B), U$1.D10 (*D10)
DIG11: IC1_SERIAL_MUX.9 (C), U$1.D11 (*D11)
DIG12: R11.2, U$1.D12
FLOW_PULSES: FLOW_SENSOR_SELECT.4, IC1.6 (O)
GND: C1.2, C2.2, C3.2, C4.2, C5.2, C6.2 (-), C7.2 (-), C8.2, FLOW_SENSOR.2, IC1.8 (VSS), IC1_SERIAL_MUX.8 (GND), IC2.4 (V-), IC2_9V_REG.GND, J1.PWR, LED1.K (C), LED2.K (C), LED3.K (C), OK1.2 (C), OK1.4 (EMI), Q1_S1.1 (S), Q2_S2.1 (S), Q3_S3.1 (S), Q4_S4.1 (S), Q5_S5.1 (S), R1.1, R2.1, R3.1, R4.1, R5.1, R9.A, U$1.GND@0 (GND), U$1.GND@1 (GND), U$1.GND@2 (GND), U$2.10 (GND)
MUX0: IC1_SERIAL_MUX.13 (X0), SV1.3
MUX1: IC1_SERIAL_MUX.14 (X1), SV2.3
MUX2: IC1_SERIAL_MUX.15 (X2), SV3.3
MUX3: IC1_SERIAL_MUX.12 (X3), SV4.3
MUX4: IC1_SERIAL_MUX.1 (X4), SV5.3
MUX5: IC1_SERIAL_MUX.5 (X5), U$2.2 (DOUT)
unnamed: Q1_S1.3 (D), SENSOR1.SLEEVE
unnamed: Q2_S2.3 (D), SENSOR2.SLEEVE
unnamed: Q3_S3.3 (D), SENSOR3.SLEEVE
unnamed: Q4_S4.3 (D), SENSOR4.SLEEVE
unnamed: Q5_S5.3 (D), SENSOR5.SLEEVE
unnamed: SENSOR1.RING, SV1.2, SV1.4, SV1.6
unnamed: SENSOR2.RING, SV2.2, SV2.4, SV2.6
unnamed: SENSOR3.RING, SV3.2, SV3.4, SV3.6
unnamed: SENSOR4.RING, SV4.2, SV4.4, SV4.6
unnamed: SENSOR5.RING, SV5.2, SV5.4, SV5.6
unnamed: FLOW_SENSOR_SELECT.6, SV5.1
unnamed: IC1.3 (I), U$1.TX
unnamed: IC1.2 (O), U$2.3 (DIN)
unnamed: R6.2, U$2.13 (DIO9)
unnamed: LED1.A, R6.1
unnamed: R7.2, U$1.D13
unnamed: LED2.A, R7.1
unnamed: C8.1, FLOW_SENSOR_SELECT.1, IC2_9V_REG.IN
unnamed: IC2.2 (-IN), R9.S
unnamed: LED3.A, R8.1
unnamed: J1.GND@1 (GNDBREAK), J1.GND@2 (GND), POWER_SELECT.4, POWER_SELECT.6
unnamed: IC1.7 (I), IC2.1 (OUT)
unnamed: FLOW_SENSOR.1, IC2.3 (+IN), R10.2
unnamed: OK1.1 (A), R11.1
unnamed: D1.A, K1.2, OK1.5 (COL)
unnamed: X1.1, X2.2
unnamed: K1.P, X2.1
unnamed: K1.S, X1.2
RX: IC1_SERIAL_MUX.3 (X), U$1.RX
VCC: IC1_SERIAL_MUX.16 (VCC)
VEE: IC1_SERIAL_MUX.7 (VEE)

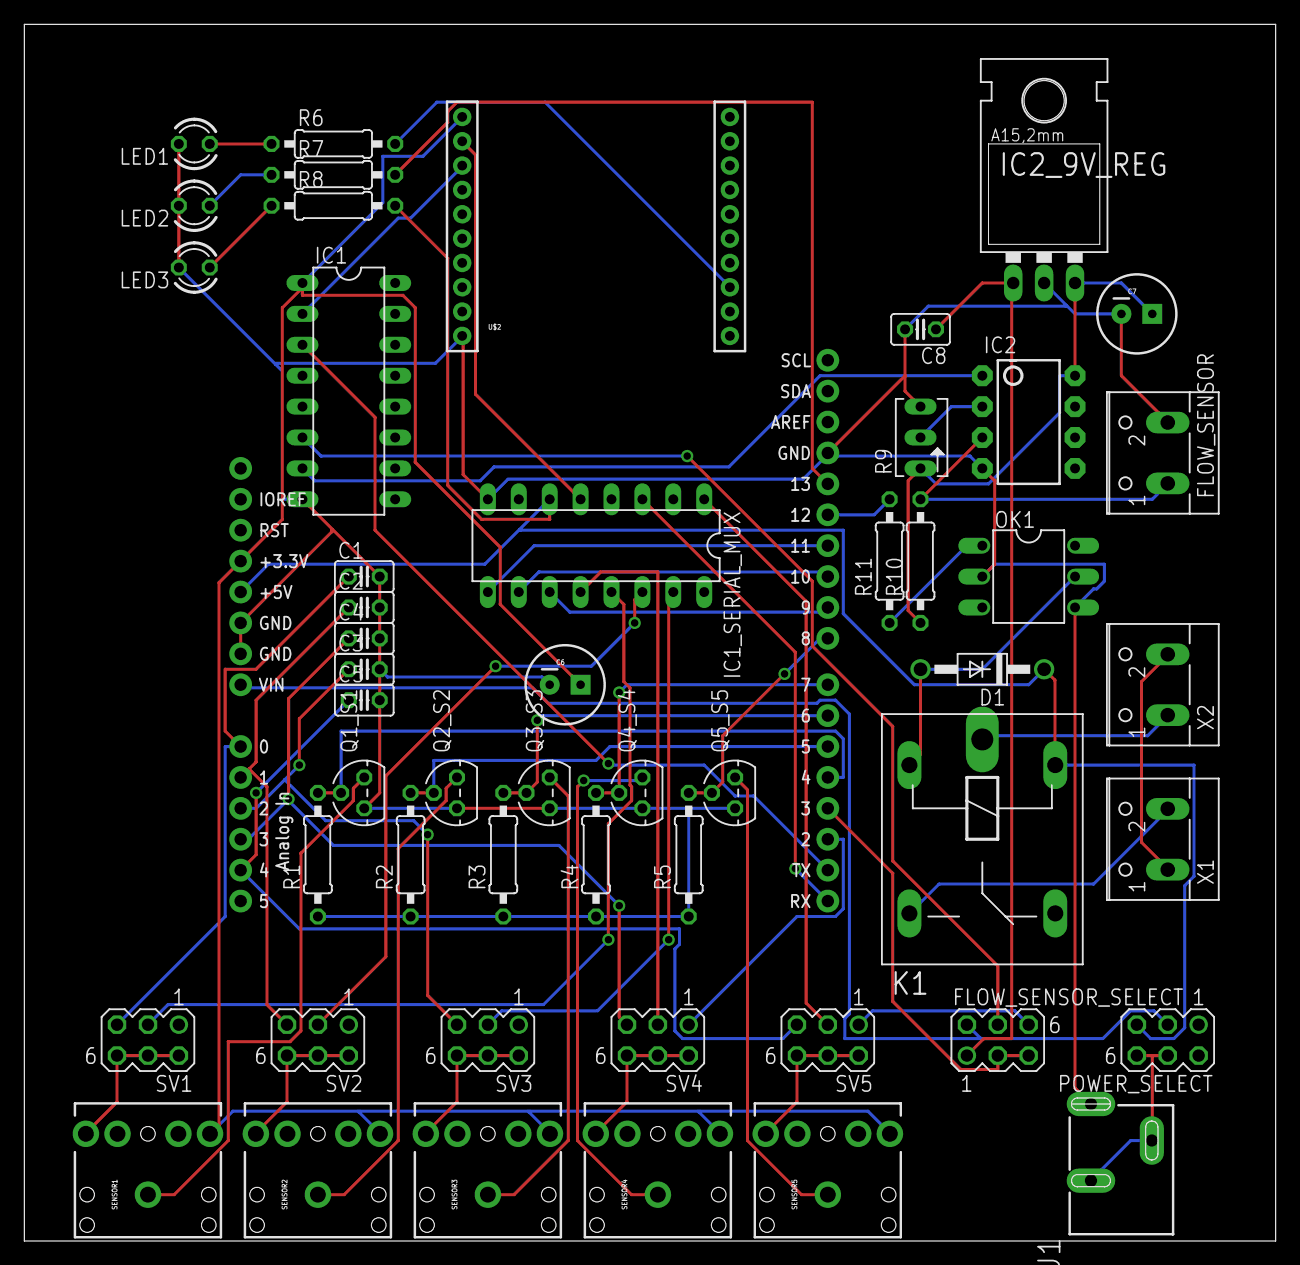
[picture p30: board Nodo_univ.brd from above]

Board: 2 copper layers, 102.9 x 100.0 mm, 52 parts (0 on the bottom side), 57 nets.

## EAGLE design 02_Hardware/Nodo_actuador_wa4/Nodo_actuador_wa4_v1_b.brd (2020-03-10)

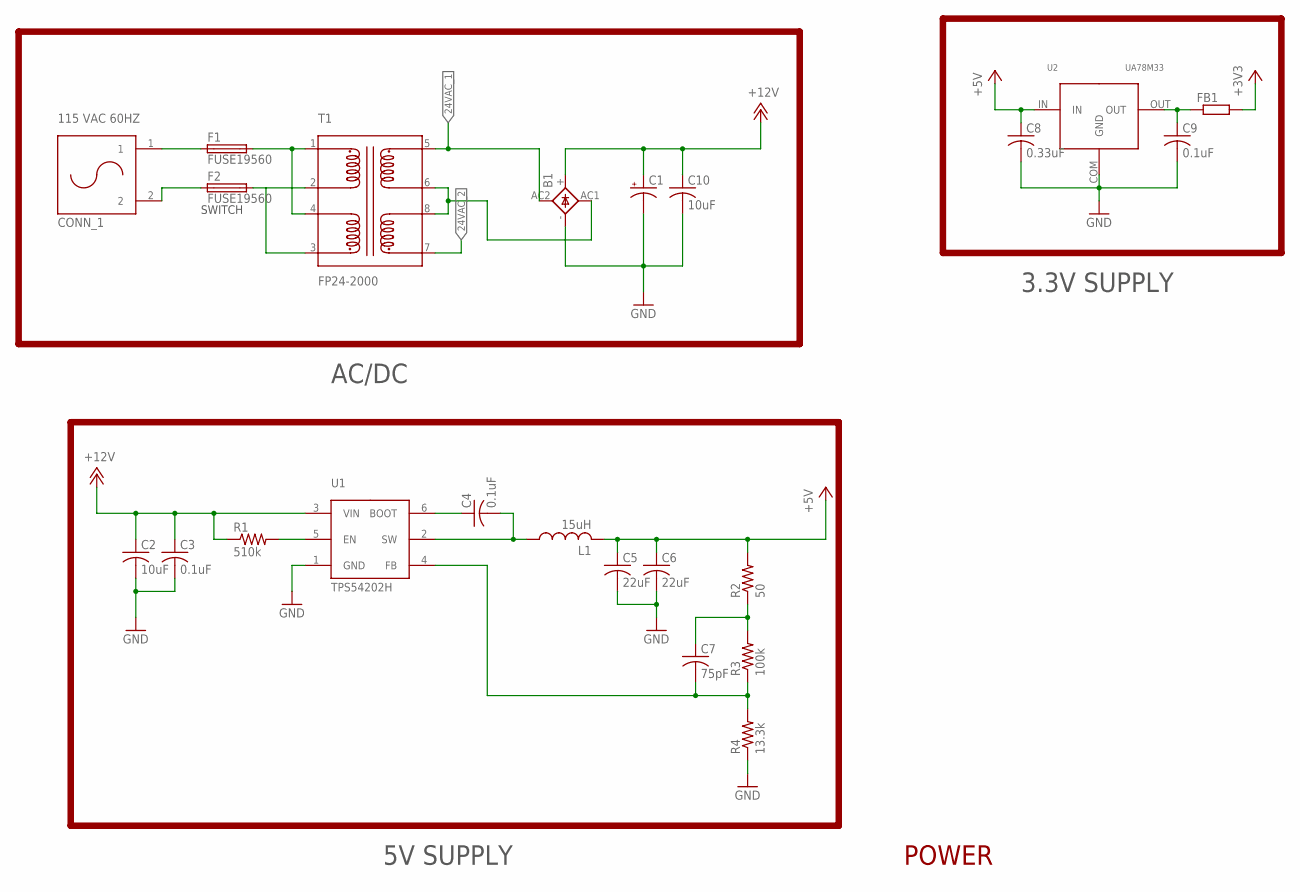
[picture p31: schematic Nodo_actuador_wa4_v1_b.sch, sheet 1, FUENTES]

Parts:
B1: GBU4; GBU4S
C1: CPOL-USE5-13; E5-13
C2, C10: 10uF; C0805
C3, C4, C9: 0.1uF; C0805
C5, C6: 22uF; C0805
C7: 75pF; C0805
C8: 0.33uF; C0805
CONN_1: 115 VAC 60HZ; 2570-2210
F1, F2: FUSE19560; 19560
FB1: R-EU_M0805; M0805
L1: 15uH; VLS5045
R1: 510k; R0805
R2: 50; R0805
R3: 100k; R0805
R4: 13.3k; R0805
T1: FP24-2000
U1: TPS54202H; SOT-23-6
U2: UA78M33; UA78XX

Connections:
24VAC_1: B1.AC2 (AC1), T1.5; also elsewhere on the board
24VAC_2: T1.7; also elsewhere on the board
+3V3: FB1.2; also elsewhere on the board
+5V: C5.1, C6.1, C8.1, L1.2, R2.2, U2.IN; also elsewhere on the board
+12V: B1.+, C1.+, C2.1, C3.1, C10.1, R1.1, U1.3 (VIN); also elsewhere on the board
GND: B1.-, C1.-, C2.2, C3.2, C5.2, C6.2, C8.2, C9.2, C10.2, R4.1, U1.1 (GND), U2.COM (GND); also elsewhere on the board
unnamed: F1.2, T1.1, T1.4
unnamed: F2.2, T1.2, T1.3
unnamed: B1.AC1 (AC2), T1.6, T1.8
unnamed: C4.1, U1.6 (BOOT)
unnamed: C4.2, L1.1, U1.2 (SW)
unnamed: R1.2, U1.5 (EN)
unnamed: C7.1, R2.1, R3.2
unnamed: C7.2, R3.1, R4.2, U1.4 (FB)
unnamed: CONN_1.1, F1.1
unnamed: CONN_1.2, F2.1
unnamed: C9.1, FB1.1, U2.OUT

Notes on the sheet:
POWER
5V SUPPLY
3.3V SUPPLY
AC/DC
SWITCH

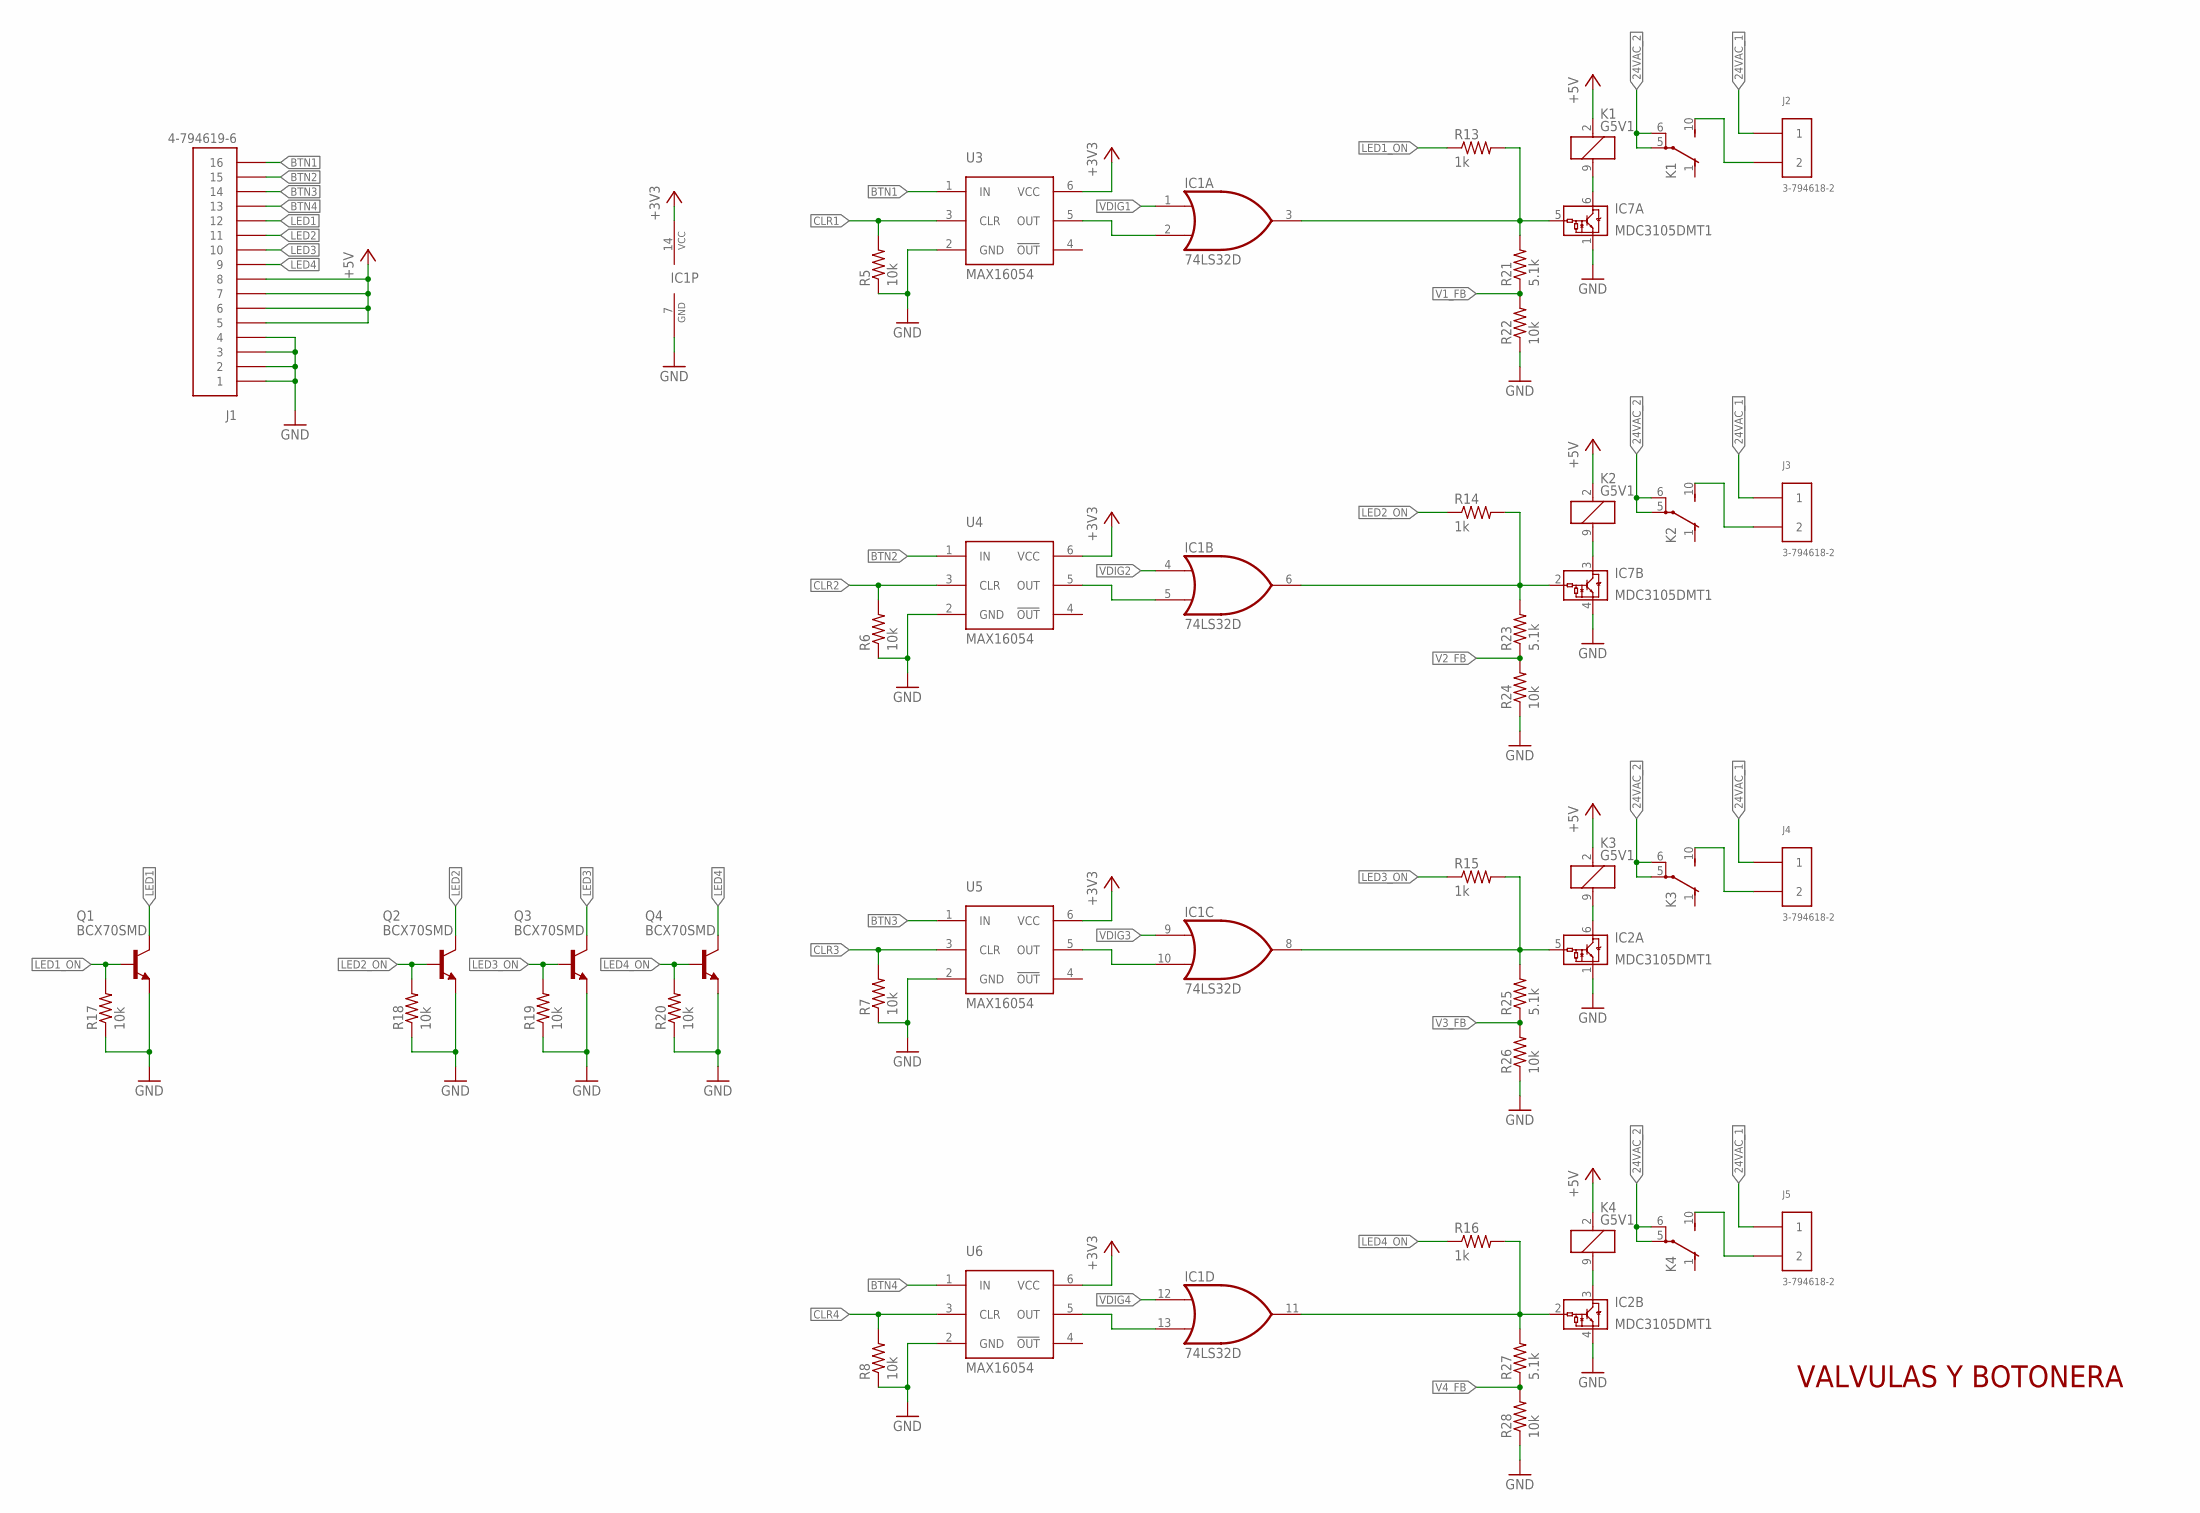
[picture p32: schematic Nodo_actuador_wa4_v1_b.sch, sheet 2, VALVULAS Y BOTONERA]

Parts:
IC1: 74LS32D; SO14
IC2, IC7: MDC3105DMT1; SC-74
J1: 4-794619-6
J2, J3, J4, J5: 3-794618-2
K1, K2, K3, K4: G5V1
Q1, Q2, Q3, Q4: BCX70SMD; SOT23
R5, R6, R7, R8, R17, R18, R19, R20, R22, R24, R26, R28: 10k; R0805
R13, R14, R15, R16: 1k; R0805
R21, R23, R25, R27: 5.1k; R0805
U3, U4, U5, U6: MAX16054; SOT-23-6

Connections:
24VAC_1: J2.1, J3.1, J4.1, J5.1; also elsewhere on the board
24VAC_2: K1.5, K1.6, K2.5, K2.6, K3.5, K3.6, K4.5, K4.6; also elsewhere on the board
+3V3: IC1.14 (VCC), U3.6 (VCC), U4.6 (VCC), U5.6 (VCC), U6.6 (VCC); also elsewhere on the board
+5V: J1.5, J1.6, J1.7, J1.8, K1.2 (1), K2.2 (1), K3.2 (1), K4.2 (1); also elsewhere on the board
BTN1: J1.16, U3.1 (IN)
BTN2: J1.15, U4.1 (IN)
BTN3: J1.14, U5.1 (IN)
BTN4: J1.13, U6.1 (IN)
CLR1: R5.2, U3.3 (CLR); also elsewhere on the board
CLR2: R6.2, U4.3 (CLR); also elsewhere on the board
CLR3: R7.2, U5.3 (CLR); also elsewhere on the board
CLR4: R8.2, U6.3 (CLR); also elsewhere on the board
GND: IC1.7 (GND), IC2.1 (GND), IC2.4 (GND), IC7.1 (GND), IC7.4 (GND), J1.1, J1.2, J1.3, J1.4, Q1.2 (E), Q2.2 (E), Q3.2 (E), Q4.2 (E), R5.1, R6.1, R7.1, R8.1, R17.1, R18.1, R19.1, R20.1, R22.1, R24.1, R26.1, R28.1, U3.2 (GND), U4.2 (GND), U5.2 (GND), U6.2 (GND); also elsewhere on the board
LED1: J1.12, Q1.3 (C)
LED1_ON: Q1.1 (B), R13.1, R17.2
LED2: J1.11, Q2.3 (C)
LED2_ON: Q2.1 (B), R14.1, R18.2
LED3: J1.10, Q3.3 (C)
LED3_ON: Q3.1 (B), R15.1, R19.2
LED4: J1.9, Q4.3 (C)
LED4_ON: Q4.1 (B), R16.1, R20.2
unnamed: IC1.2 (I1), U3.5 (OUT)
unnamed: IC1.5 (I1), U4.5 (OUT)
unnamed: IC1.10 (I1), U5.5 (OUT)
unnamed: IC1.13 (I1), U6.5 (OUT)
unnamed: IC1.3 (O), IC7.5 (VIN), R13.2, R21.2
unnamed: IC7.6 (VOUT), K1.9 (2)
unnamed: IC7.3 (VOUT), K2.9 (2)
unnamed: IC1.8 (O), IC2.5 (VIN), R15.2, R25.2
unnamed: IC2.6 (VOUT), K3.9 (2)
unnamed: IC1.11 (O), IC2.2 (VIN), R16.2, R27.2
unnamed: IC2.3 (VOUT), K4.9 (2)
unnamed: J2.2, K1.10 (S)
unnamed: J3.2, K2.10 (S)
unnamed: J4.2, K3.10 (S)
unnamed: J5.2, K4.10 (S)
unnamed: IC1.6 (O), IC7.2 (VIN), R14.2, R23.2
V1_FB: R21.1, R22.2; also elsewhere on the board
V2_FB: R23.1, R24.2; also elsewhere on the board
V3_FB: R25.1, R26.2; also elsewhere on the board
V4_FB: R27.1, R28.2; also elsewhere on the board
VDIG1: IC1.1 (I0); also elsewhere on the board
VDIG2: IC1.4 (I0); also elsewhere on the board
VDIG3: IC1.9 (I0); also elsewhere on the board
VDIG4: IC1.12 (I0); also elsewhere on the board

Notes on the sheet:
VALVULAS Y BOTONERA

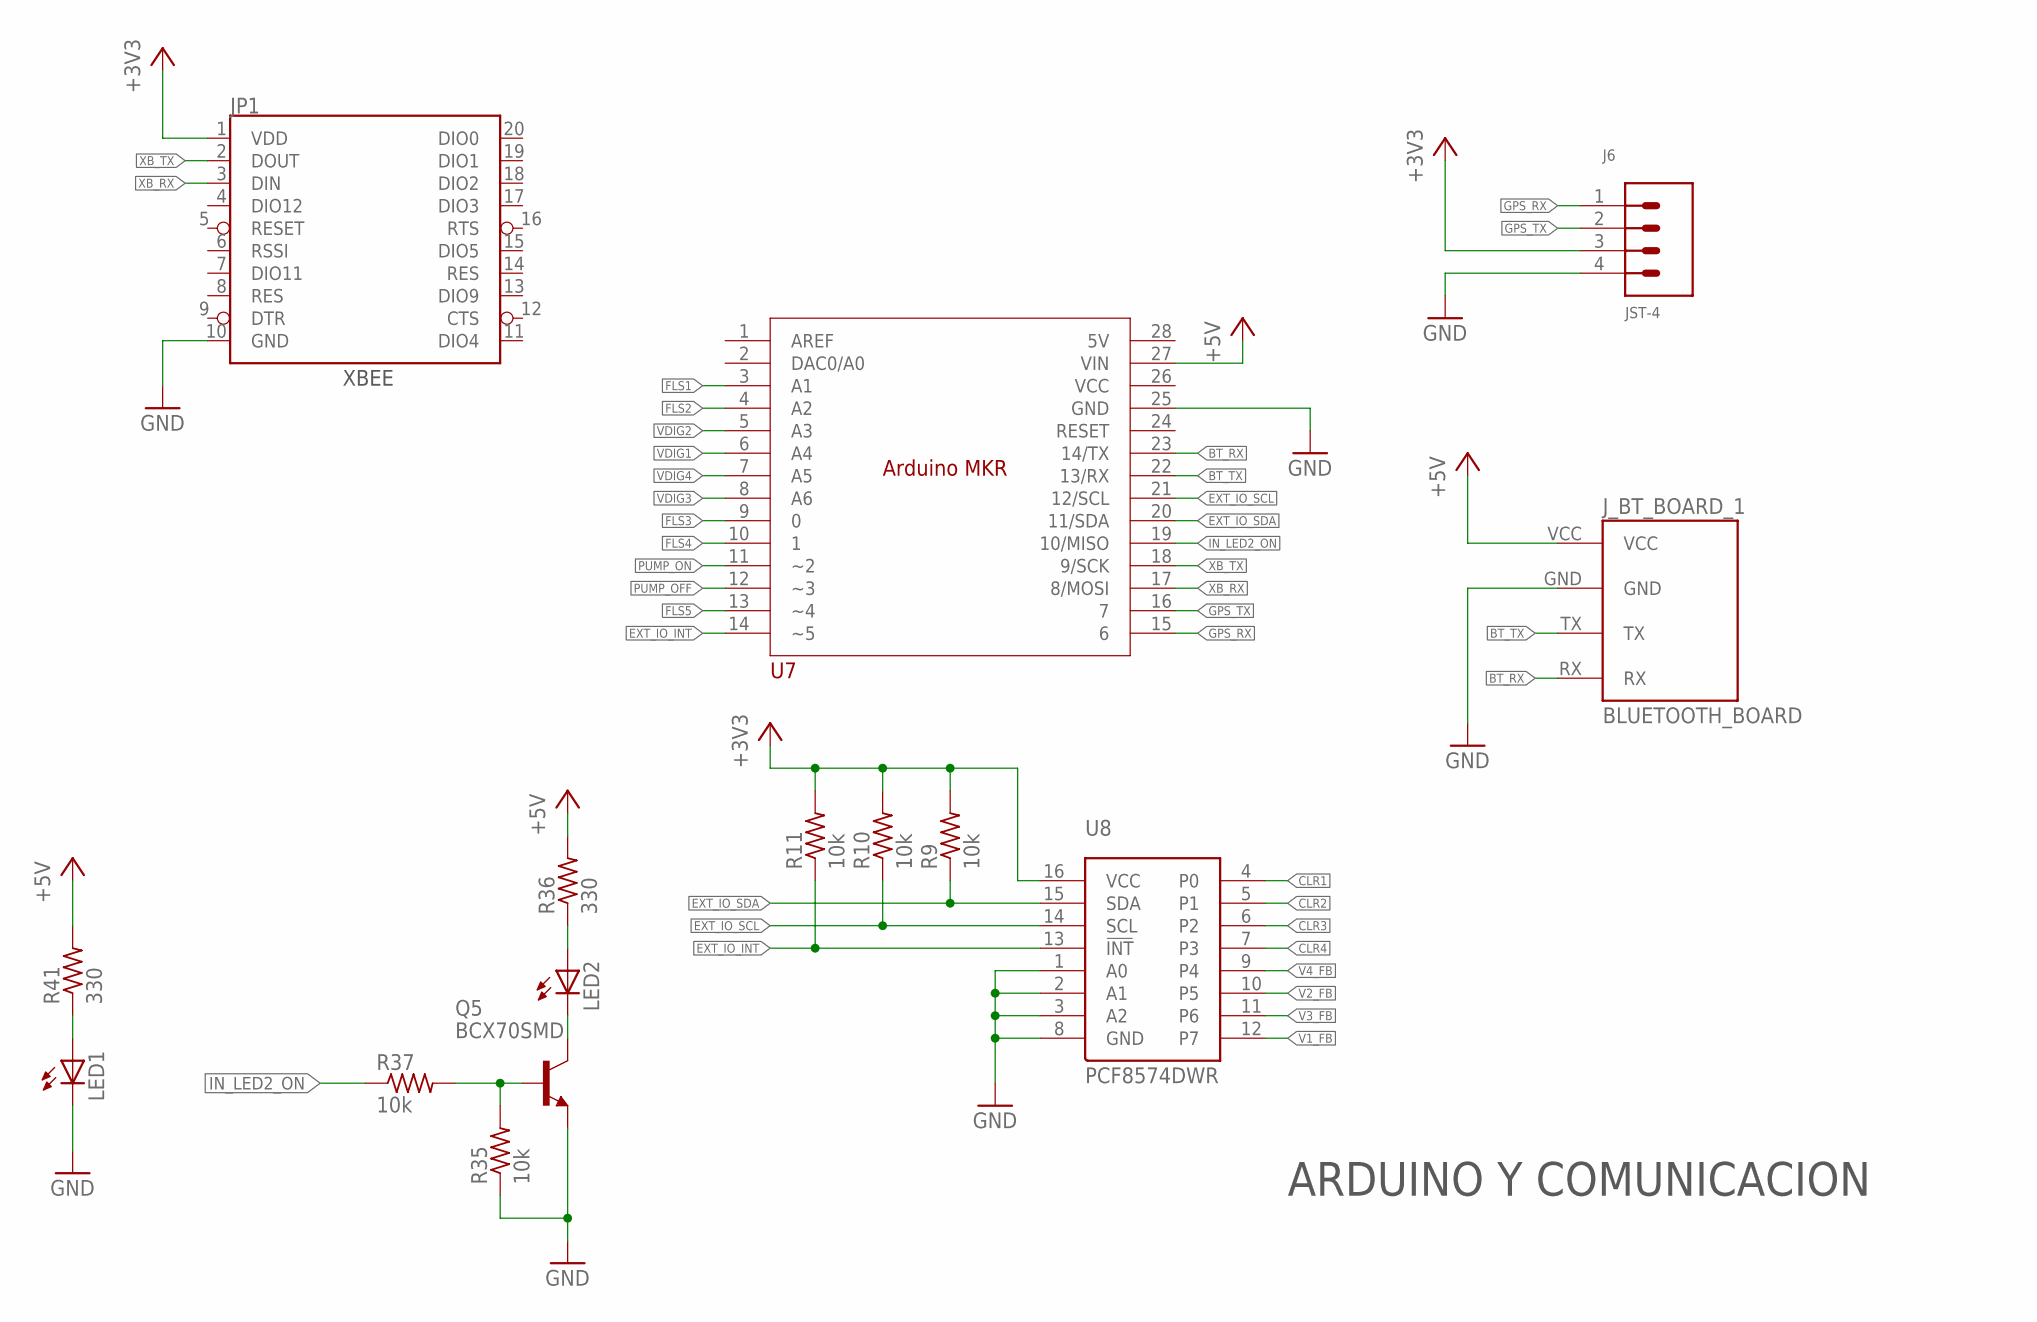
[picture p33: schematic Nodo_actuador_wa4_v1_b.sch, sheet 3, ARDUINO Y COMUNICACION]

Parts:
J6: JST-4
JP1: XBEESILK; XBEE-SILK
J_BT_BOARD_1: BLUETOOTH_BOARD; BT_BOARD_FOOTPRINT
LED1, LED2: LEDCHIP-LED0805; CHIP-LED0805
Q5: BCX70SMD; SOT23
R9, R10, R11, R35, R37: 10k; R0805
R36, R41: 330; R0805
U7: ARDUINO_MKR
U8: PCF8574DWR; SOIC16_1

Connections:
+3V3: J6.3, JP1.1 (VDD), R9.2, R10.2, R11.2, U8.16 (VCC); also elsewhere on the board
+5V: J_BT_BOARD_1.VCC, R36.2, R41.2, U7.27 (VIN); also elsewhere on the board
BT_RX: J_BT_BOARD_1.RX, U7.23 (14/TX)
BT_TX: J_BT_BOARD_1.TX, U7.22 (13/RX)
CLR1: U8.4 (P0); also elsewhere on the board
CLR2: U8.5 (P1); also elsewhere on the board
CLR3: U8.6 (P2); also elsewhere on the board
CLR4: U8.7 (P3); also elsewhere on the board
EXT_IO_INT: R11.1, U7.14 (~5), U8.13 (!INT)
EXT_IO_SCL: R10.1, U7.21 (12/SCL), U8.14 (SCL)
EXT_IO_SDA: R9.1, U7.20 (11/SDA), U8.15 (SDA)
FLS1: U7.3 (A1); also elsewhere on the board
FLS2: U7.4 (A2); also elsewhere on the board
FLS3: U7.9 (0); also elsewhere on the board
FLS4: U7.10 (1); also elsewhere on the board
FLS5: U7.13 (~4); also elsewhere on the board
GND: J6.4, JP1.10 (GND), J_BT_BOARD_1.GND, LED1.C, Q5.2 (E), R35.1, U7.25 (GND), U8.1 (A0), U8.2 (A1), U8.3 (A2), U8.8 (GND); also elsewhere on the board
GPS_RX: J6.1, U7.15 (6)
GPS_TX: J6.2, U7.16 (7)
IN_LED2_ON: R37.1, U7.19 (10/MISO)
unnamed: LED2.A, R36.1
unnamed: LED2.C, Q5.3 (C)
unnamed: LED1.A, R41.1
unnamed: Q5.1 (B), R35.2, R37.2
PUMP_OFF: U7.12 (~3); also elsewhere on the board
PUMP_ON: U7.11 (~2); also elsewhere on the board
V1_FB: U8.12 (P7); also elsewhere on the board
V2_FB: U8.10 (P5); also elsewhere on the board
V3_FB: U8.11 (P6); also elsewhere on the board
V4_FB: U8.9 (P4); also elsewhere on the board
VDIG1: U7.6 (A4); also elsewhere on the board
VDIG2: U7.5 (A3); also elsewhere on the board
VDIG3: U7.8 (A6); also elsewhere on the board
VDIG4: U7.7 (A5); also elsewhere on the board
XB_RX: JP1.3 (DIN), U7.17 (8/MOSI)
XB_TX: JP1.2 (DOUT), U7.18 (9/SCK)

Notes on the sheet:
ARDUINO Y COMUNICACION
XBEE

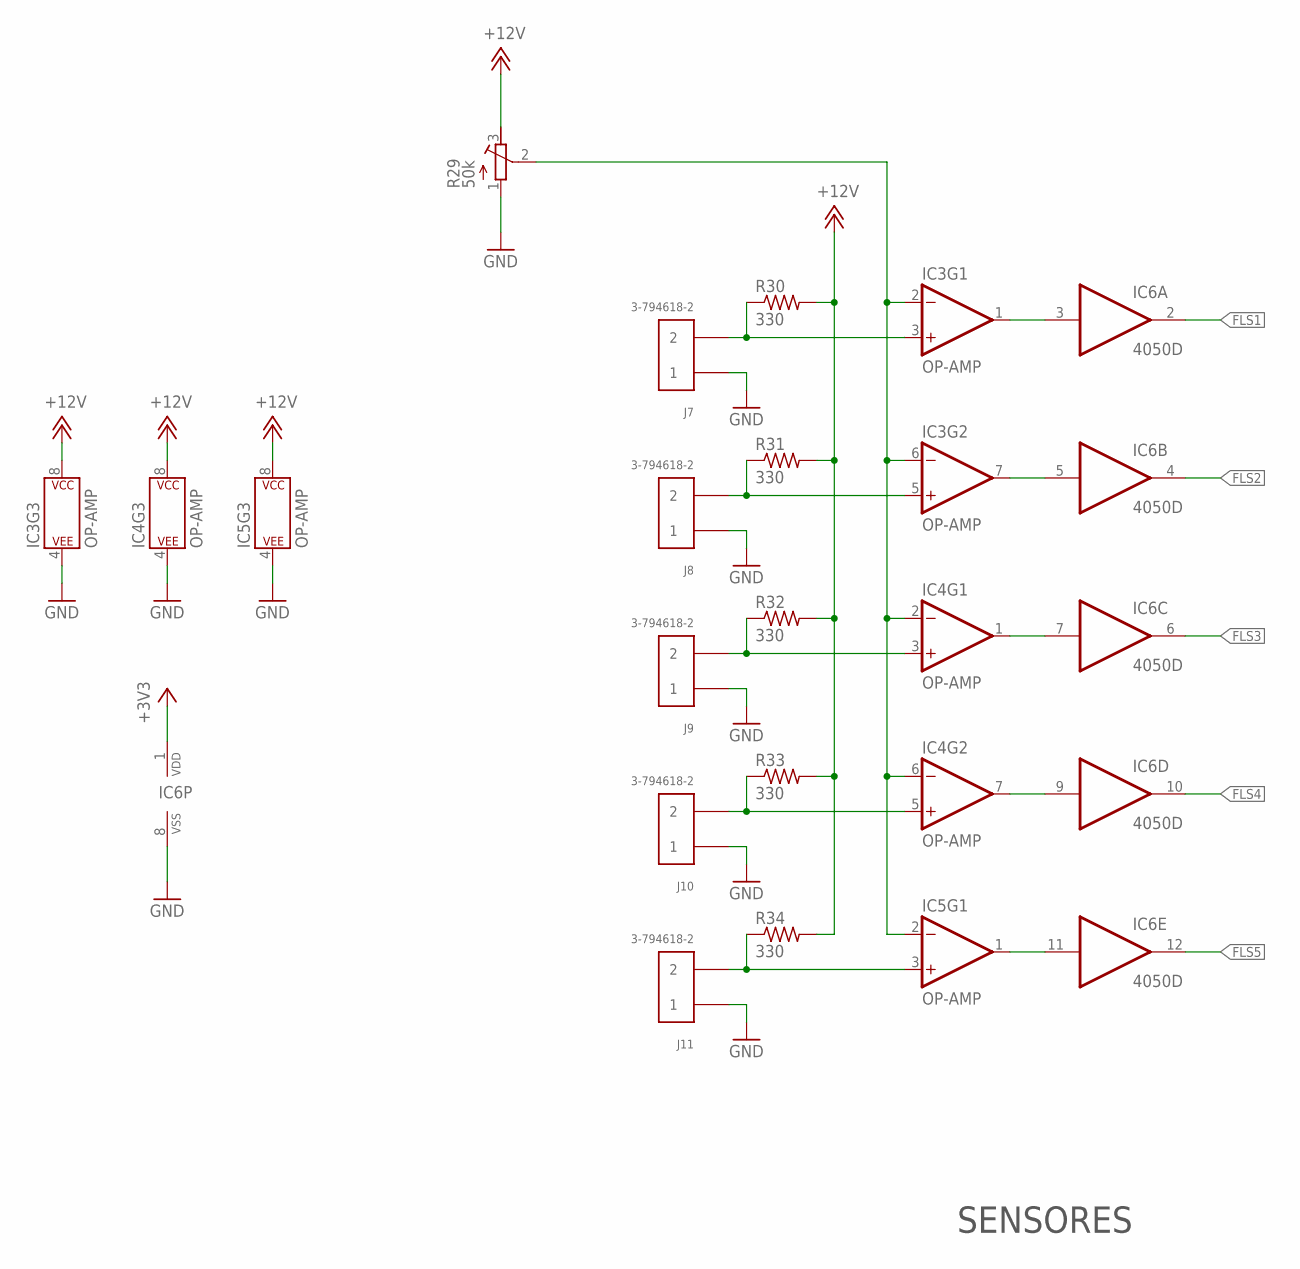
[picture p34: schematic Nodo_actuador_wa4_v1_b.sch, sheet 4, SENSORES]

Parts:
IC3, IC4, IC5: OP-AMP; SO08
IC6: 4050D; SO16
J7, J8, J9, J10, J11: 3-794618-2
R29: 50k; RTRIM3224W
R30, R31, R32, R33, R34: 330; R0805

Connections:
+3V3: IC6.1 (VDD); also elsewhere on the board
+12V: IC3.8 (P$V+), IC4.8 (P$V+), IC5.8 (P$V+), R29.3 (E), R30.2, R31.2, R32.2, R33.2, R34.2; also elsewhere on the board
FLS1: IC6.2 (O); also elsewhere on the board
FLS2: IC6.4 (O); also elsewhere on the board
FLS3: IC6.6 (O); also elsewhere on the board
FLS4: IC6.10 (O); also elsewhere on the board
FLS5: IC6.12 (O); also elsewhere on the board
GND: IC3.4 (P$V-), IC4.4 (P$V-), IC5.4 (P$V-), IC6.8 (VSS), J7.1, J8.1, J9.1, J10.1, J11.1, R29.1 (A); also elsewhere on the board
unnamed: IC3.3 (+IN), J7.2, R30.1
unnamed: IC3.5 (+IN), J8.2, R31.1
unnamed: IC4.3 (+IN), J9.2, R32.1
unnamed: IC4.5 (+IN), J10.2, R33.1
unnamed: IC5.3 (+IN), J11.2, R34.1
unnamed: IC3.1 (OUT), IC6.3 (I)
unnamed: IC3.7 (OUT), IC6.5 (I)
unnamed: IC4.1 (OUT), IC6.7 (I)
unnamed: IC4.7 (OUT), IC6.9 (I)
unnamed: IC5.1 (OUT), IC6.11 (I)
SENSOR_VREF: IC3.2 (-IN), IC3.6 (-IN), IC4.2 (-IN), IC4.6 (-IN), IC5.2 (-IN), R29.2 (S)

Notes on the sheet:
SENSORES

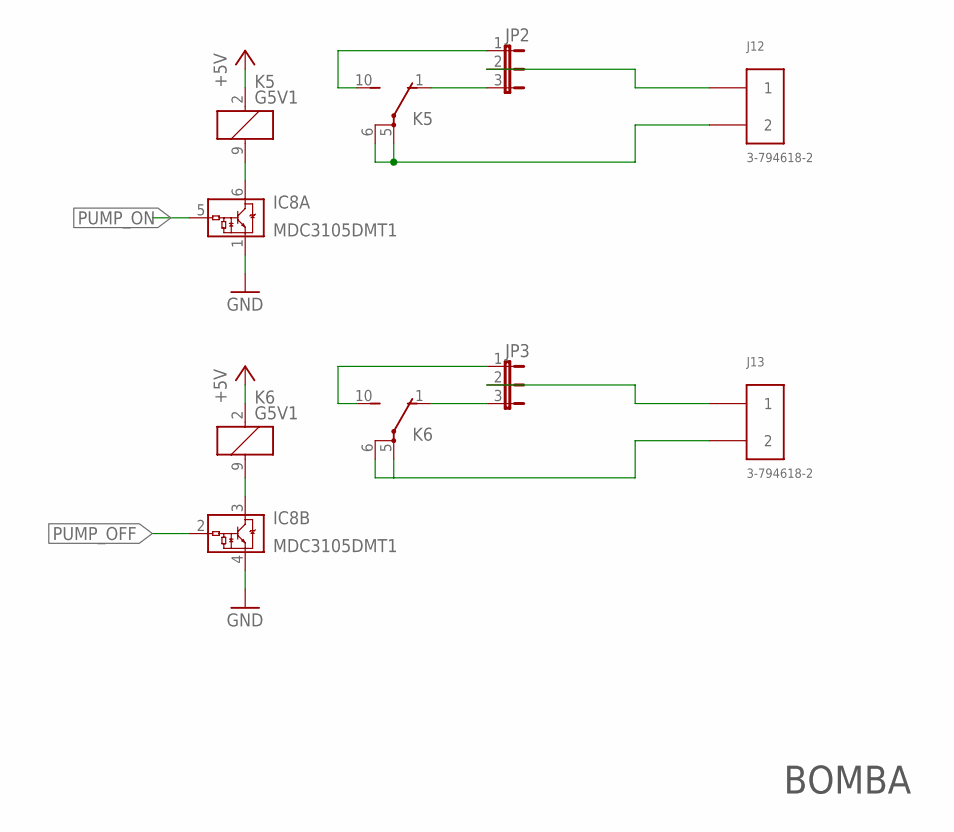
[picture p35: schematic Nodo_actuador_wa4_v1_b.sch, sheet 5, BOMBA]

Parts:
IC8: MDC3105DMT1; SC-74
J12, J13: 3-794618-2
JP2, JP3: JP2E; JP2
K5, K6: G5V1

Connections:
+5V: K5.2 (1), K6.2 (1); also elsewhere on the board
GND: IC8.1 (GND), IC8.4 (GND); also elsewhere on the board
unnamed: IC8.6 (VOUT), K5.9 (2)
unnamed: JP2.1, K5.10 (S)
unnamed: JP2.3, K5.1 (O)
unnamed: J12.1, JP2.2
unnamed: J12.2, K5.5, K5.6
unnamed: J13.1, JP3.2
unnamed: J13.2, K6.5, K6.6
unnamed: JP3.1, K6.10 (S)
unnamed: JP3.3, K6.1 (O)
unnamed: IC8.3 (VOUT), K6.9 (2)
PUMP_OFF: IC8.2 (VIN); also elsewhere on the board
PUMP_ON: IC8.5 (VIN); also elsewhere on the board

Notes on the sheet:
BOMBA

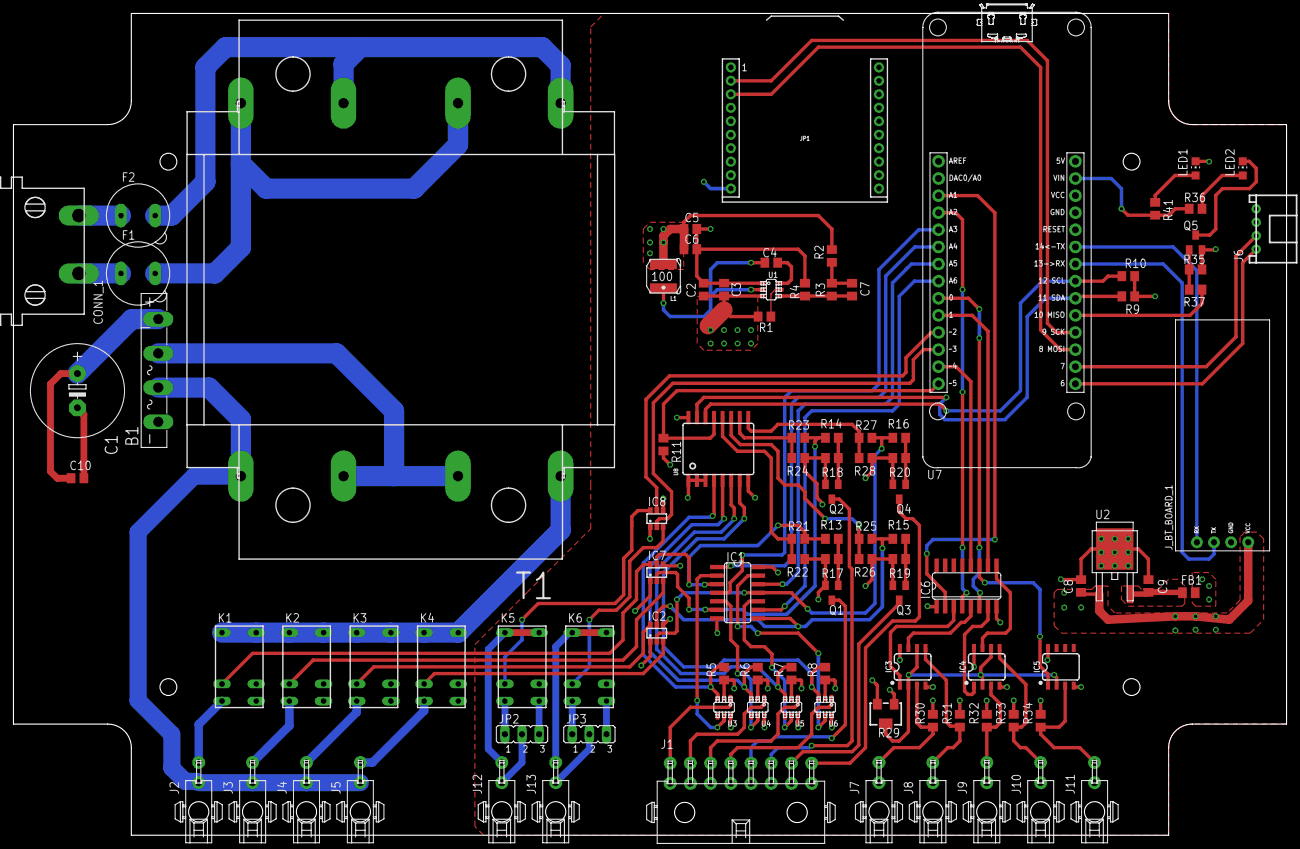
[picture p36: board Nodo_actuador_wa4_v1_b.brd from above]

Board: 4 copper layers, 189.0 x 122.0 mm, 100 parts (0 on the bottom side), 99 nets.

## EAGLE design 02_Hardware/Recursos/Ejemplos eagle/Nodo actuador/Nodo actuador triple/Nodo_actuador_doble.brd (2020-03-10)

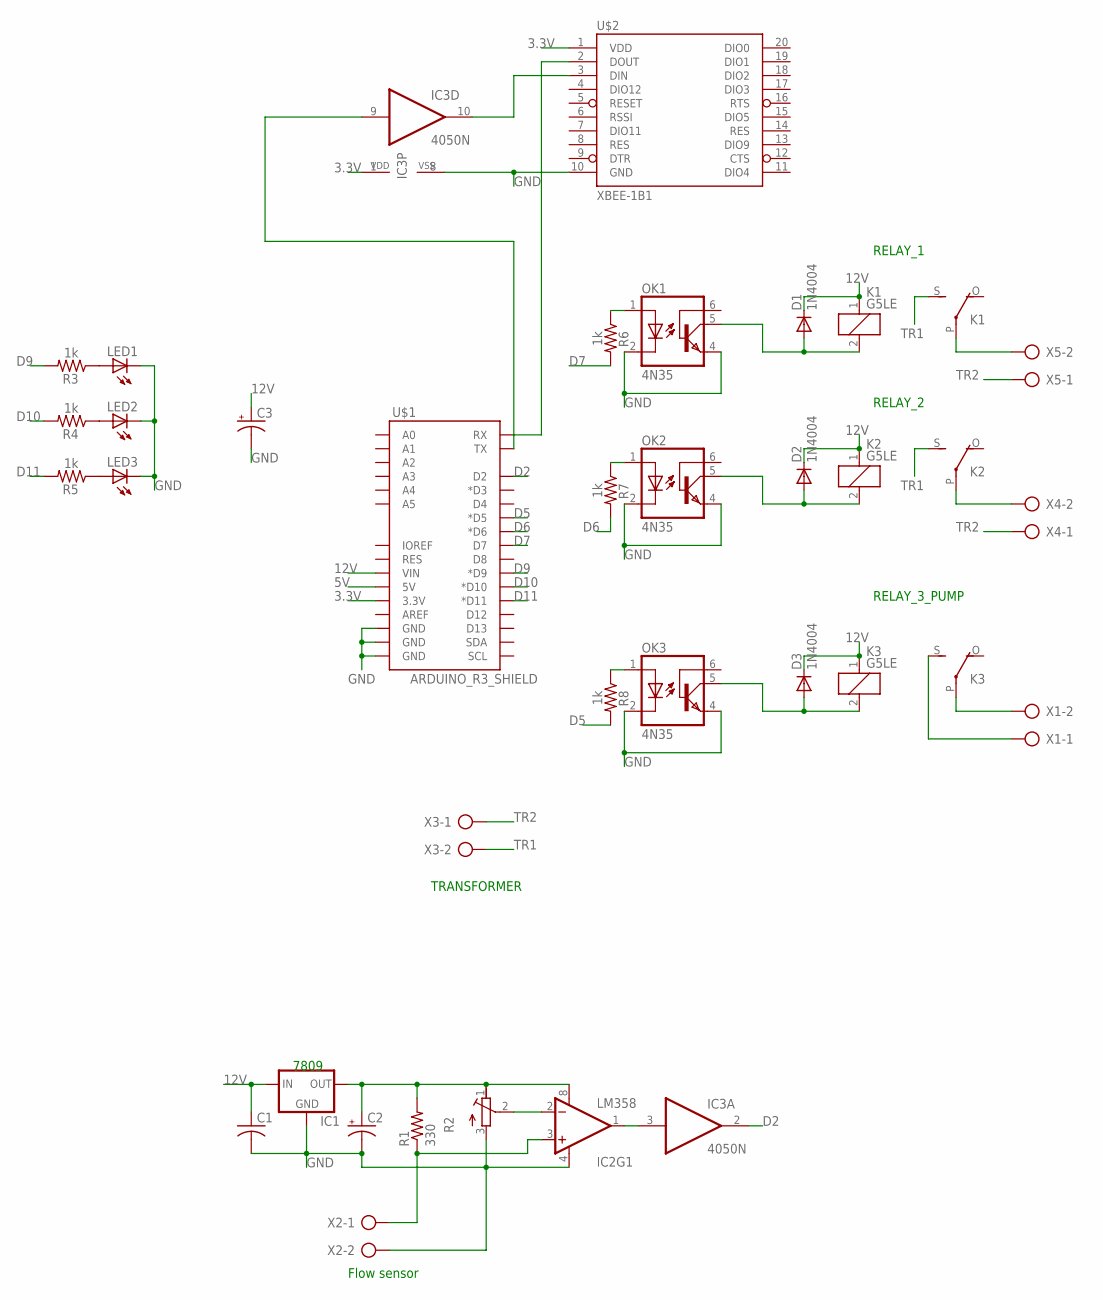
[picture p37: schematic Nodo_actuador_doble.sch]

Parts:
C1: C-US050-024X044; C050-024X044
C2, C3: CPOL-USE2.5-6; E2,5-6
D1, D2, D3: 1N4004; DO41-10
IC1: 78XXS
IC2: LM358; DIP08
IC3: 4050N; DIL16
K1, K2, K3: G5LE
LED1, LED2, LED3: LED3MM
OK1, OK2, OK3: 4N35; DIL06
R1: 330; 0204/7
R2: R-TRIMMT93YA; RTRIMT93YA
R3, R4, R5, R6, R7, R8: 1k; 0204/7
U$1: ARDUINO_R3_SHIELD; UNO_R3_SHIELD
U$2: XBEE-1B1; XBEE-1
X1, X2, X3, X4, X5: AK500/2

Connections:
3.3V: IC3.1 (VDD), U$1.3.3V, U$2.1 (VDD)
5V: U$1.5V
12V: C1.1, C3.+, D1.C, D2.C, D3.C, IC1.IN, K1.1, K2.1, K3.1, U$1.VIN
D2: IC3.2 (O), U$1.D2
D5: R8.2, U$1.D5 (*D5)
D6: R7.2, U$1.D6 (*D6)
D7: R6.2, U$1.D7
D9: R3.2, U$1.D9 (*D9)
D10: R4.2, U$1.D10 (*D10)
D11: R5.2, U$1.D11 (*D11)
GND: C1.2, C2.-, C3.-, IC1.GND, IC2.4 (V-), IC3.8 (VSS), LED1.K (C), LED2.K (C), LED3.K (C), OK1.2 (C), OK1.4 (EMI), OK2.2 (C), OK2.4 (EMI), OK3.2 (C), OK3.4 (EMI), R2.3 (E), U$1.GND@0 (GND), U$1.GND@1 (GND), U$1.GND@2 (GND), U$2.10 (GND), X2.2
unnamed: LED1.A, R3.1
unnamed: LED2.A, R4.1
unnamed: LED3.A, R5.1
unnamed: IC2.3 (+IN), R1.1, X2.1
unnamed: C2.+, IC1.OUT, IC2.8 (V+), R1.2, R2.1 (A)
unnamed: IC2.1 (OUT), IC3.3 (I)
unnamed: IC2.2 (-IN), R2.2 (S)
unnamed: K1.P, X5.2
unnamed: D1.A, K1.2, OK1.5 (COL)
unnamed: K2.P, X4.2
unnamed: D2.A, K2.2, OK2.5 (COL)
unnamed: U$1.RX, U$2.2 (DOUT)
unnamed: IC3.9 (I), U$1.TX
unnamed: IC3.10 (O), U$2.3 (DIN)
unnamed: D3.A, K3.2, OK3.5 (COL)
unnamed: K3.P, X1.2
unnamed: K3.S, X1.1
unnamed: OK1.1 (A), R6.1
unnamed: OK2.1 (A), R7.1
unnamed: OK3.1 (A), R8.1
TR1: K1.S, K2.S, X3.2
TR2: X3.1, X4.1, X5.1

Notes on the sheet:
7809
Flow sensor
TRANSFORMER
RELAY_1
RELAY_2
RELAY_3_PUMP

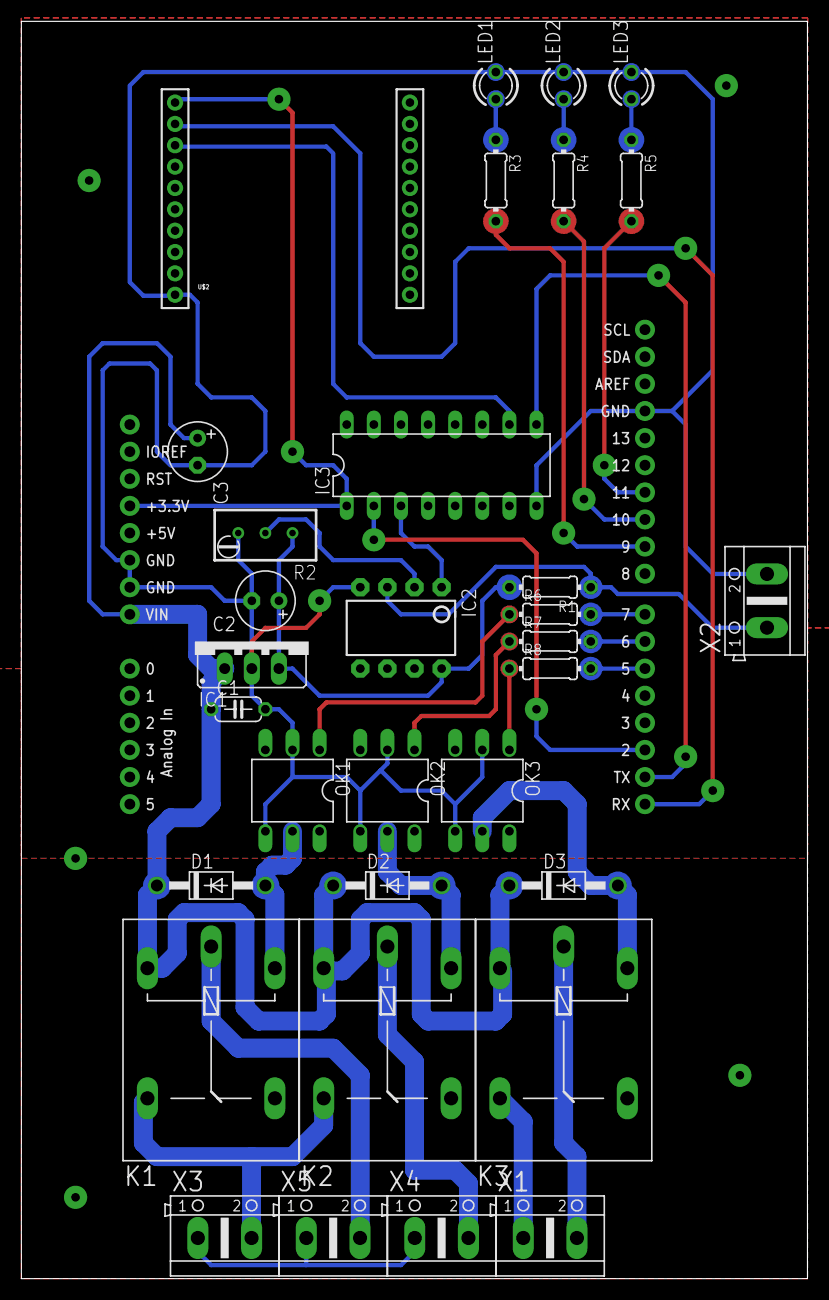
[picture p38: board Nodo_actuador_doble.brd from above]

Board: 2 copper layers, 73.6 x 117.8 mm, 33 parts (0 on the bottom side), 32 nets.

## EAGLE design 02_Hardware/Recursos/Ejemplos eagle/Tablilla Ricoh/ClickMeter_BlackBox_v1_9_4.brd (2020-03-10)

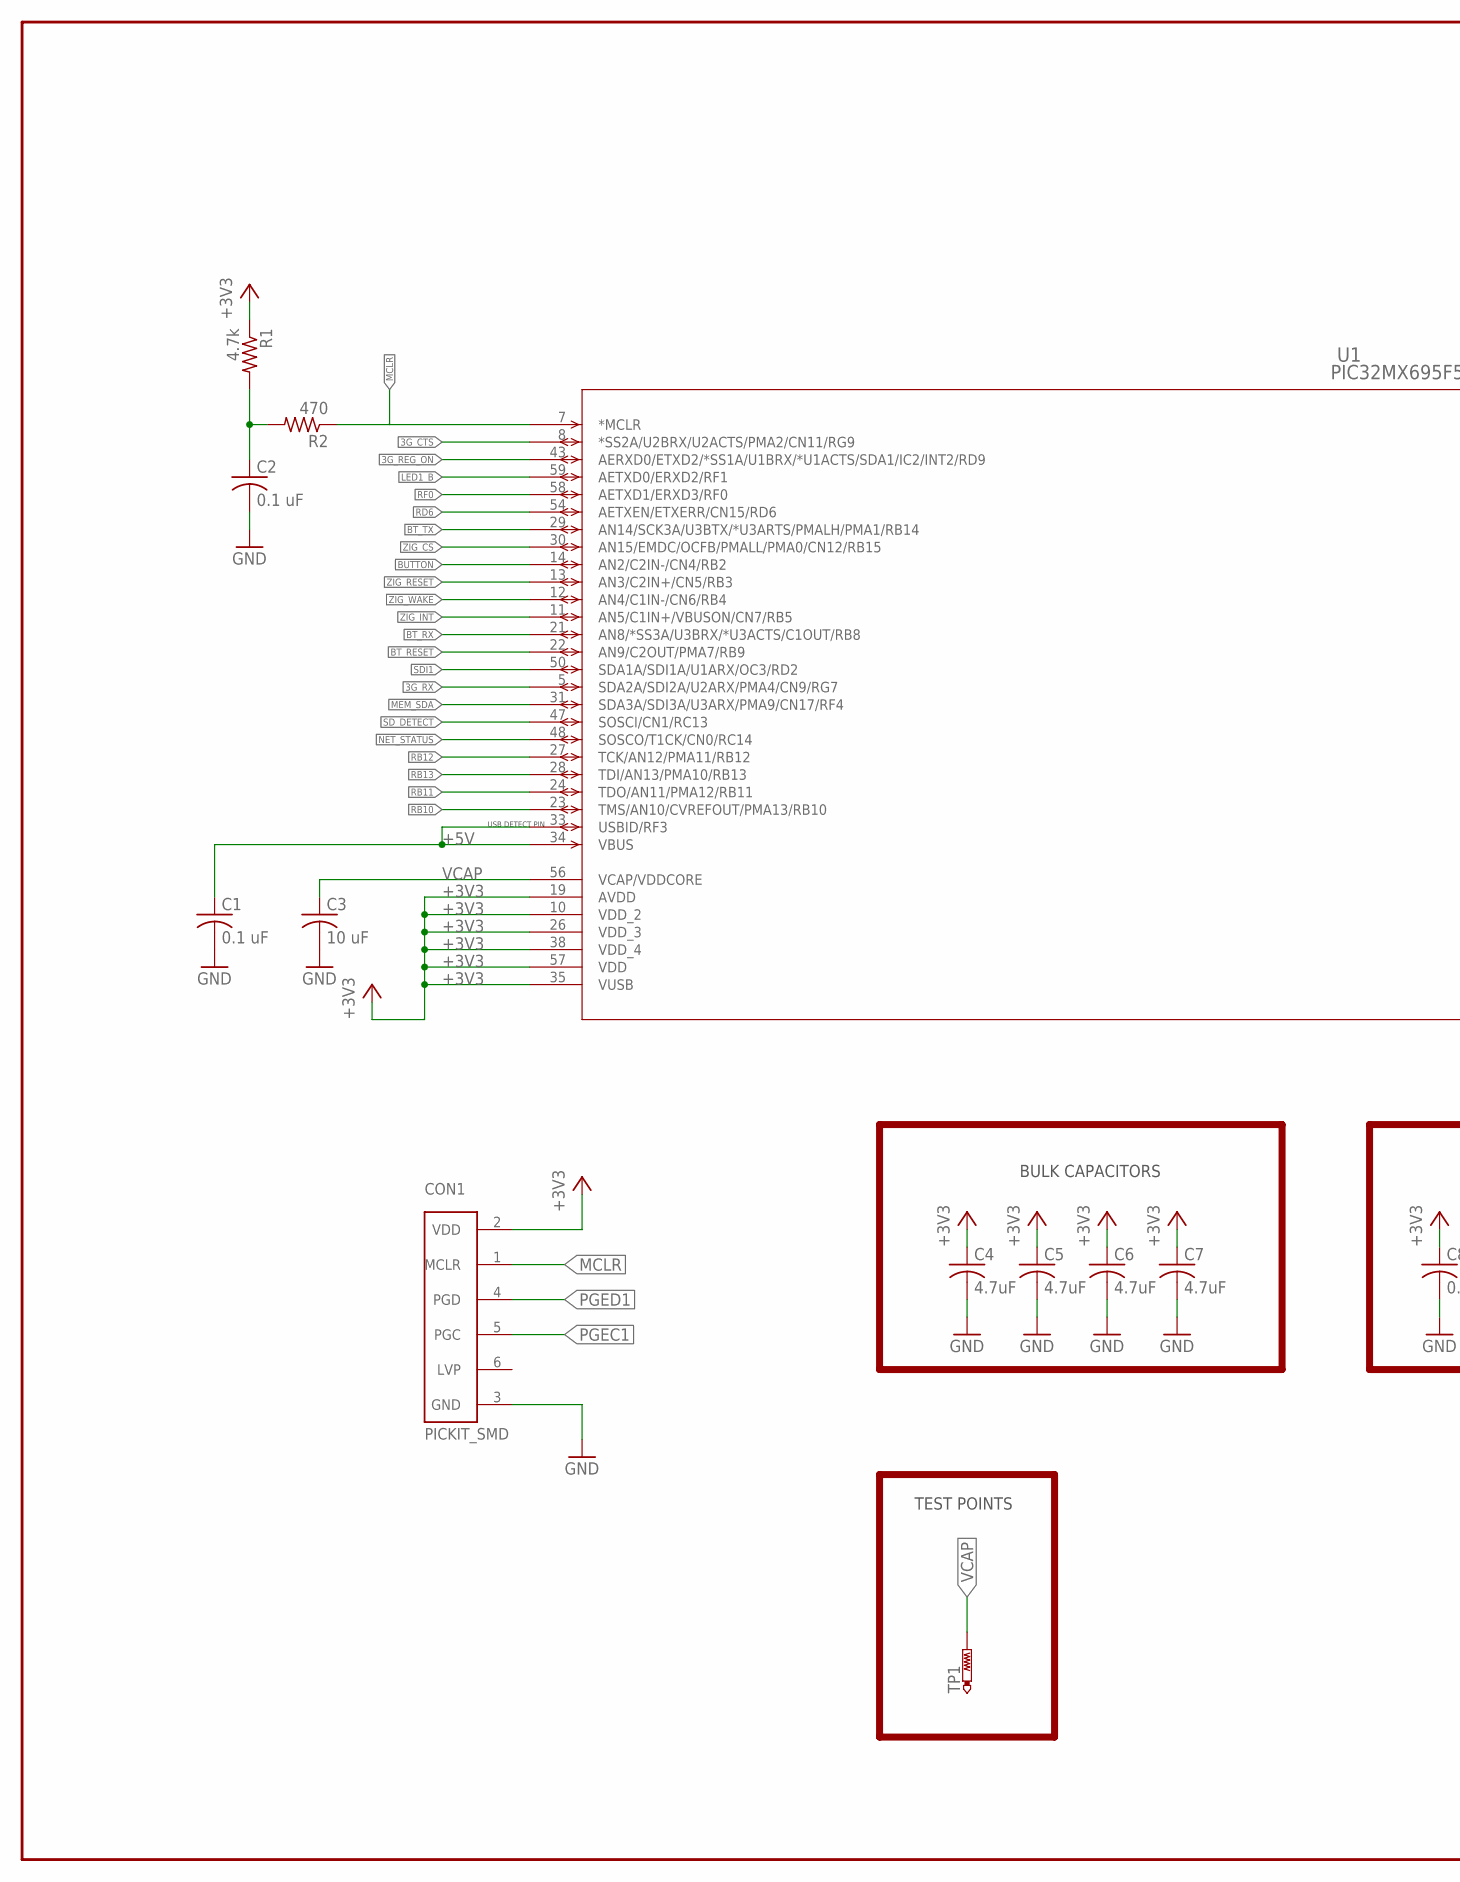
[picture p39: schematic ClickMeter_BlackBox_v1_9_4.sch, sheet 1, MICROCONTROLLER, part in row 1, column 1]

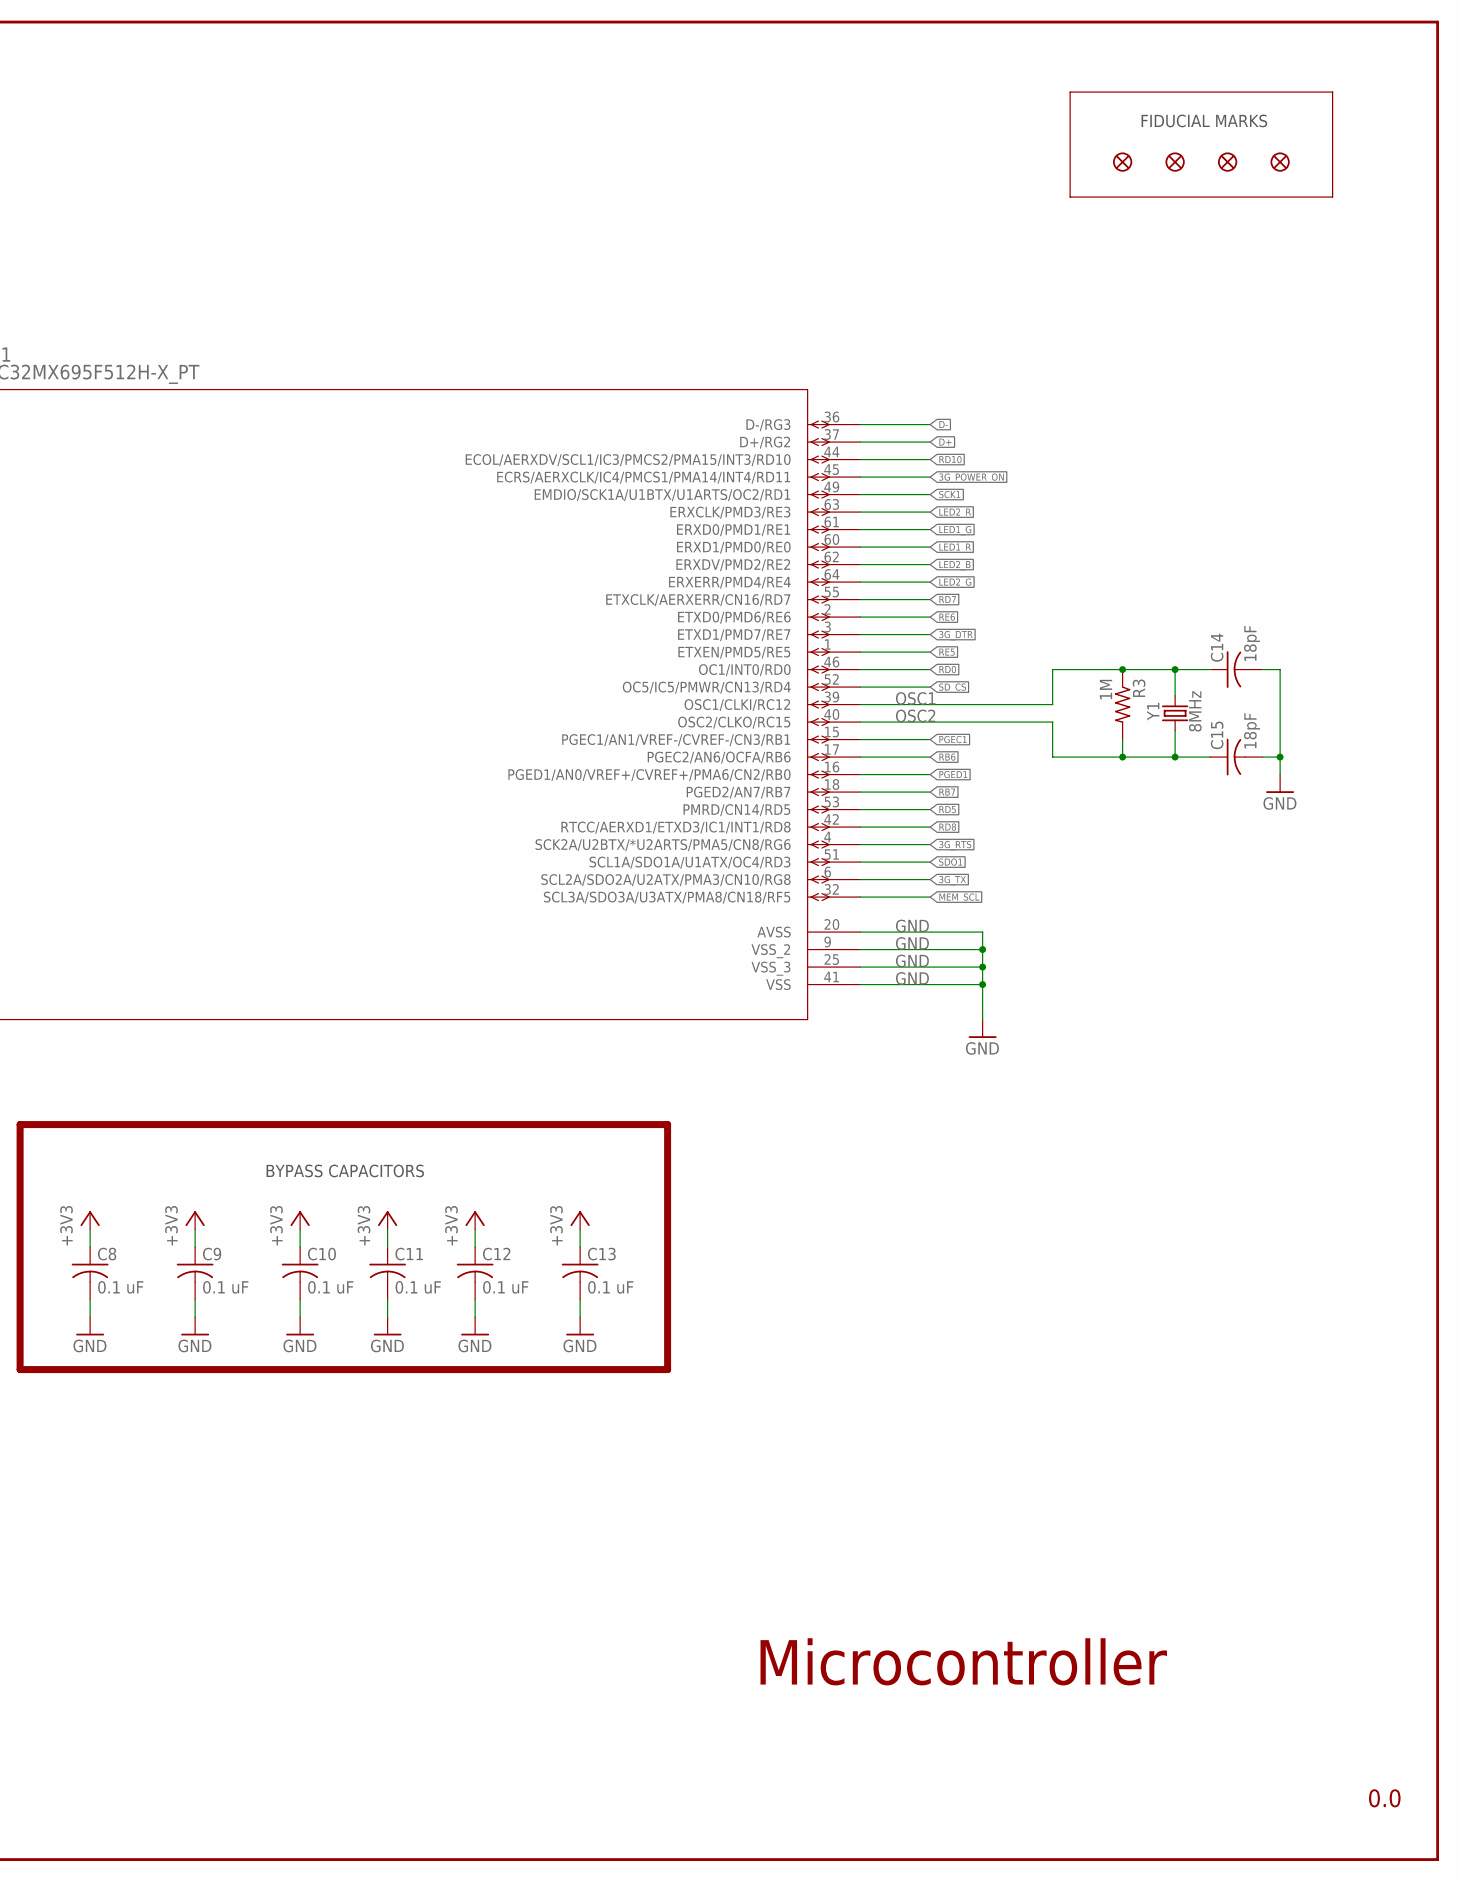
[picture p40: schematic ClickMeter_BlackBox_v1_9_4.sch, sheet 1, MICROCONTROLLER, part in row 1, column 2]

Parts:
C1, C2, C8, C9, C10, C11, C12, C13: 0.1 uF; C0603
C3: 10 uF; C0805
C4, C5, C6, C7: 4.7uF; C0603
C14, C15: 18pF; C0603
CON1: PICKIT_SMD; SMD_PICKIT
F1, F2, F3, F4: FIDUCIAL
R1: 4.7k; R0603
R2: 470; R0603
R3: 1M; R0603
TP1: PTR1B1,27; B1,27
U1: PIC32MX695F512H-X_PT; TQFP64_10X10MC
Y1: 8MHz; CRYSTAL-TXC-7A

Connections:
3G_CTS: U1.8 (*SS2A/U2BRX/U2ACTS/PMA2/CN11/RG9); also elsewhere on the board
3G_DTR: U1.3 (ETXD1/PMD7/RE7); also elsewhere on the board
3G_POWER_ON: U1.45 (ECRS/AERXCLK/IC4/PMCS1/PMA14/INT4/RD11); also elsewhere on the board
3G_REG_ON: U1.43 (AERXD0/ETXD2/*SS1A/U1BRX/*U1ACTS/SDA1/I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)
3G_RTS: U1.4 (SCK2A/U2BTX/*U2ARTS/PMA5/CN8/RG6); also elsewhere on the board
3G_RX: U1.5 (SDA2A/SDI2A/U2ARX/PMA4/CN9/RG7); also elsewhere on the board
3G_TX: U1.6 (SCL2A/SDO2A/U2ATX/PMA3/CN10/RG8); also elsewhere on the board
+3V3: C4.1, C5.1, C6.1, C7.1, C8.1, C9.1, C10.1, C11.1, C12.1, C13.1, CON1.2 (VDD), R1.1, U1.10 (VDD_2), U1.19 (AVDD), U1.26 (VDD_3), U1.35 (VUSB), U1.38 (VDD_4), U1.57 (VDD); also elsewhere on the board
+5V: C1.1, U1.33 (USBID/RF3), U1.34 (VBUS); also elsewhere on the board
BT_RESET: U1.22 (AN9/C2OUT/PMA7/RB9); also elsewhere on the board
BT_RX: U1.21 (AN8/*SS3A/U3BRX/*U3ACTS/C1OUT/RB8); also elsewhere on the board
BT_TX: U1.29 (AN14/SCK3A/U3BTX/*U3ARTS/PMALH/PMA1/RB14); also elsewhere on the board
BUTTON: U1.14 (AN2/C2IN-/CN4/RB2); also elsewhere on the board
D+: U1.37 (D+/RG2); also elsewhere on the board
D-: U1.36 (D-/RG3); also elsewhere on the board
GND: C1.2, C2.2, C3.2, C4.2, C5.2, C6.2, C7.2, C8.2, C9.2, C10.2, C11.2, C12.2, C13.2, C14.2, C15.2, CON1.3 (GND), U1.9 (VSS_2), U1.20 (AVSS), U1.25 (VSS_3), U1.41 (VSS); also elsewhere on the board
LED1_B: U1.59 (AETXD0/ERXD2/RF1); also elsewhere on the board
LED1_G: U1.61 (ERXD0/PMD1/RE1); also elsewhere on the board
LED1_R: U1.60 (ERXD1/PMD0/RE0); also elsewhere on the board
LED2_B: U1.62 (ERXDV/PMD2/RE2); also elsewhere on the board
LED2_G: U1.64 (ERXERR/PMD4/RE4); also elsewhere on the board
LED2_R: U1.63 (ERXCLK/PMD3/RE3); also elsewhere on the board
MCLR: CON1.1 (MCLR), R2.1, U1.7 (*MCLR)
MEM_SCL: U1.32 (SCL3A/SDO3A/U3ATX/PMA8/CN18/RF5); also elsewhere on the board
MEM_SDA: U1.31 (SDA3A/SDI3A/U3ARX/PMA9/CN17/RF4); also elsewhere on the board
unnamed: C2.1, R1.2, R2.2
NET_STATUS: U1.48 (SOSCO/T1CK/CN0/RC14); also elsewhere on the board
OSC1: C14.1, R3.1, U1.39 (OSC1/CLKI/RC12), Y1.P$2 (2)
OSC2: C15.1, R3.2, U1.40 (OSC2/CLKO/RC15), Y1.P$1 (1)
PGEC1: CON1.5 (PGC), U1.15 (PGEC1/AN1/VREF-/CVREF-/CN3/RB1)
PGED1: CON1.4 (PGD), U1.16 (PGED1/AN0/VREF+/CVREF+/PMA6/CN2/RB0)
RB6: U1.17 (PGEC2/AN6/OCFA/RB6)
RB7: U1.18 (PGED2/AN7/RB7)
RB10: U1.23 (TMS/AN10/CVREFOUT/PMA13/RB10)
RB11: U1.24 (TDO/AN11/PMA12/RB11)
RB12: U1.27 (TCK/AN12/PMA11/RB12)
RB13: U1.28 (TDI/AN13/PMA10/RB13)
RD0: U1.46 (OC1/INT0/RD0)
RD5: U1.53 (PMRD/CN14/RD5)
RD6: U1.54 (AETXEN/ETXERR/CN15/RD6)
RD7: U1.55 (ETXCLK/AERXERR/CN16/RD7)
RD8: U1.42 (RTCC/AERXD1/ETXD3/IC1/INT1/RD8)
RD10: U1.44 (ECOL/AERXDV/SCL1/IC3/PMCS2/PMA15/INT3/R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)
RE5: U1.1 (ETXEN/PMD5/RE5)
RE6: U1.2 (ETXD0/PMD6/RE6)
RF0: U1.58 (AETXD1/ERXD3/RF0)
SCK1: U1.49 (EMDIO/SCK1A/U1BTX/U1ARTS/OC2/RD1); also elsewhere on the board
SDI1: U1.50 (SDA1A/SDI1A/U1ARX/OC3/RD2); also elsewhere on the board
SDO1: U1.51 (SCL1A/SDO1A/U1ATX/OC4/RD3); also elsewhere on the board
SD_CS: U1.52 (OC5/IC5/PMWR/CN13/RD4); also elsewhere on the board
SD_DETECT: U1.47 (SOSCI/CN1/RC13); also elsewhere on the board
VCAP: C3.1, TP1.TP, U1.56 (VCAP/VDDCORE)
ZIG_CS: U1.30 (AN15/EMDC/OCFB/PMALL/PMA0/CN12/RB15)
ZIG_INT: U1.11 (AN5/C1IN+/VBUSON/CN7/RB5)
ZIG_RESET: U1.13 (AN3/C2IN+/CN5/RB3)
ZIG_WAKE: U1.12 (AN4/C1IN-/CN6/RB4)

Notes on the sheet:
BULK CAPACITORS
BYPASS CAPACITORS
Microcontroller
0.0
USB DETECT PIN
FIDUCIAL MARKS
TEST POINTS


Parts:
C16, C19: 10 uF; C0805
C17, C18: 1uF; C0603
C20: 0.1uF; C0603
C21: 150uF; C1210
CON2: 47346-1001
FB1, FB2, FB3, FB4, FB5: FB; 0603
IC1: LP38501; TO-263-5
IC2: MIC5504-3.3YM5-TR; SOT-23-5
IC3: TPS2041CDBVR; SOT-23-5
IC4: SN65220DBVR; SOT-23-6
Q1: BSR15; SOT23
R4: 56k; R0603
R5: 10k; R0603
R6: 10; R2010
R7, R8: 27; R0603
R9, R10: 15k; R0603
R11: 4.7k; R0603
R12: 47k; R0603
R13: 100; R0603
TP2, TP3, TP4, TP5, TP6, TP7: PTR1B1,27; B1,27

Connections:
+3V3: C18.1, IC2.5 (OUT), TP4.TP; also elsewhere on the board
+3V9: FB1.1, Q1.2 (E), TP3.TP; also elsewhere on the board
+5V: C16.1, C17.1, C21.1, FB3.1, IC1.1 (EN), IC1.2 (IN), IC2.1 (IN), IC2.3 (EN), R11.1, TP2.TP; also elsewhere on the board
D+: R8.1; also elsewhere on the board
D-: R7.1; also elsewhere on the board
GND: C16.2, C17.2, C18.2, C19.2, C20.2, C21.2, FB4.2, FB5.2, IC1.3 (GND), IC1.6 (B_PAD), IC2.2 (GND), IC3.2 (GND), IC3.4 (!EN!), IC4.2 (GND), IC4.5 (GND), R5.2, R9.1, R10.2, R12.2, R13.2, TP5.TP, TP6.TP, TP7.TP; also elsewhere on the board
unnamed: C19.1, FB1.2, IC1.4 (OUT), R4.1
unnamed: IC1.5 (ADJ), R4.2, R5.1
unnamed: CON2.1 (VBUS), FB2.2
unnamed: FB3.2, IC3.1 (OUT), R6.2
unnamed: Q1.1 (B), R11.2, R12.1
unnamed: Q1.3 (C), R13.1
unnamed: CON2.S1 (SH), CON2.S2 (SH), CON2.S3 (SH), CON2.S4 (SH), CON2.S5 (SH), CON2.S6 (SH), FB5.1
unnamed: CON2.5 (GND), FB4.1
unnamed: CON2.2 (D-), IC4.4 (B), R7.2, R9.2
unnamed: CON2.3 (D+), IC4.6 (A), R8.2, R10.1
VBUS: C20.1, FB2.1, IC3.5 (IN), R6.1

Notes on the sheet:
3.3V POWER SUPPLY
10uF Capacitors: X7R Dielectric: GRM32DR71C106KA01L C3216X7R1C106K160AC
3.9V POWER SUPPLY
Ferrite
CURRENT LIMIT SWITCH
USB POWER SUPPLY AND DATA
POWER SUPPLIES AND USB
CAPACITOR DISCHARGE
TEST POINTS
TCJB157M006R0055


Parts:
C22: 0.1 uF; C0603
C23: 33pF; C0603
C24: 0.1uF; C0603
CON3: MOLEX_78646-3001
CON4: MOLEX_503182-1852
IC5: SMF05CT2G; SC-88/SC70-6/SOT-363
R14, R15, R16: 22; R0603
R17, R18, R19, R20: 10k; R0603

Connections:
+3V3: C24.1, CON4.4 (VDD), R17.2, R18.2, R19.2, R20.2; also elsewhere on the board
GND: C22.2, C23.2, C24.2, CON3.C5 (GND), CON3.GND1 (GND), CON3.GND2 (GND), CON3.GND3 (GND), CON3.GND4 (GND), CON3.GND5 (GND), CON3.GND6 (GND), CON4.6 (VSS), CON4.DET, IC5.2 (AN); also elsewhere on the board
unnamed: CON3.C3 (CLK), IC5.6 (C5), R14.1
unnamed: CON3.C7 (I/O), IC5.5 (C4), R15.1
unnamed: CON3.C2 (RST), IC5.4 (C3), R16.1
SCK1: CON4.5 (CLK/SCLK); also elsewhere on the board
SDI1: CON4.7 (DATA0/DO), R20.1; also elsewhere on the board
SDO1: CON4.3 (CMD/DI), R19.1; also elsewhere on the board
SD_CS: CON4.2 (CD/DATA3/CS), R18.1; also elsewhere on the board
SD_DETECT: CON4.SW, R17.1; also elsewhere on the board
SIM_RESET: R16.2; also elsewhere on the board
USIM_CLK: R14.2; also elsewhere on the board
USIM_DATA: R15.2; also elsewhere on the board
V_USIM: C22.1, C23.1, CON3.C1 (VCC), IC5.1 (C1); also elsewhere on the board

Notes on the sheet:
SIM CARD SOCKET
MICRO SD SOCKET
MICRO SIM/MICRO SD


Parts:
BT1: PTS525_SM15; PTS525SM15SMTR2
LED1, LED2: APTF1616SEEZGQBDC
R21: 10k; R0603
R22, R24, R25, R27: 180; R0603
R23, R26: 680; R0603

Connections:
+3V3: BT1.3, BT1.4, LED1.1, LED2.1; also elsewhere on the board
BUTTON: BT1.1, BT1.2, R21.2; also elsewhere on the board
GND: R21.1; also elsewhere on the board
LED1_B: R22.1; also elsewhere on the board
LED1_G: R23.1; also elsewhere on the board
LED1_R: R24.1; also elsewhere on the board
LED2_B: R25.1; also elsewhere on the board
LED2_G: R26.1; also elsewhere on the board
LED2_R: R27.1; also elsewhere on the board
unnamed: LED1.3, R23.2
unnamed: LED1.2, R24.2
unnamed: LED1.4, R22.2
unnamed: LED2.3, R26.2
unnamed: LED2.2, R27.2
unnamed: LED2.4, R25.2

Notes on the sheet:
FEEDBACK AND INPUT
LED FEEDBACK
BUTTON


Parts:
C25, C26, C27, C28: 1uF; C0603
J1: CC-DEBUG-P05; CC-P05
R28: 10k; R0603
U2: BLE112-VISUAL-A; BLE112-A

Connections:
+3V3: C25.1, C26.1, C27.1, C28.1, J1.2 (3V3), R28.2, U2.AVDD, U2.AVDD@2 (AVDD), U2.DVDD, U2.VDD_USB; also elsewhere on the board
BT_RESET: J1.7 (RES), R28.1, U2.RESET; also elsewhere on the board
BT_RX: U2.P1_6; also elsewhere on the board
BT_TX: U2.P1_7; also elsewhere on the board
CC_DC: J1.3 (DC), U2.P2_2
CC_DD: J1.4 (DD), U2.P2_1
GND: C25.2, C26.2, C27.2, C28.2, J1.1 (GND), U2.GND, U2.GND@2 (GND), U2.GND@3 (GND), U2.GND@4 (GND); also elsewhere on the board

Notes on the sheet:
BLUETOOTH

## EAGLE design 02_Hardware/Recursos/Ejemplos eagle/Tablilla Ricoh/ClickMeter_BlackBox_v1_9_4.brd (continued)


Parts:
ANT1: 1575AT43A0040E
C29, C30: 0.1uF; C0603
C31: 2200uF; 592D-2200
CON5: A-1JA
LED3: LED_ESML0603; LED_SML0603
Q2, Q3: BCX70SMD; SOT23
R29: 4.7k; R0603
R30: 47k; R0603
R31, R32: 10k; R0603
R33: 470; R0603
R34, R35, R36, R37: 1k; R0402
R38, R39: R-US_R0402; R0402
U3: SIM5320A

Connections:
3G_CTS: R37.1; also elsewhere on the board
3G_DTR: U3.P$72 (UART_DTR); also elsewhere on the board
3G_POWER_ON: R29.1; also elsewhere on the board
3G_RTS: R36.1; also elsewhere on the board
3G_RX: R34.1; also elsewhere on the board
3G_TX: R35.1; also elsewhere on the board
+3V9: C29.1, C30.1, C31.1, R33.2, U3.P$38 (VBAT_BB), U3.P$39 (VBAT_BB), U3.P$62 (VBAT_RF), U3.P$63 (VBAT_RF); also elsewhere on the board
GND: C29.2, C30.2, C31.2, CON5.2 (GND), CON5.3 (GND), Q2.2 (E), Q3.2 (E), R30.2, R32.2, R39.2, U3.P$1 (GND), U3.P$2 (GND), U3.P$5 (GND), U3.P$10 (GND), U3.P$14 (GND), U3.P$37 (GND), U3.P$40 (GND), U3.P$41 (GND), U3.P$43 (GND), U3.P$57 (GND), U3.P$58 (GND), U3.P$60 (GND), U3.P$61 (GND), U3.P$64 (GND), U3.P$65 (GND), U3.P$77 (GND), U3.P$78 (GND), U3.P$80 (GND); also elsewhere on the board
GPS_ANT: R38.2, U3.P$79 (GPS_ANT)
MAIN_ANT: CON5.1 (FEED), U3.P$59 (MAIN_ANT)
unnamed: R34.2, U3.P$71 (UART_TXD)
unnamed: Q2.1 (B), R29.2, R30.1
unnamed: Q3.1 (B), R31.2, R32.1
unnamed: LED3.A, R33.1
unnamed: LED3.C, Q3.3 (C)
unnamed: ANT1.FEED, R38.1, R39.1
unnamed: R35.2, U3.P$68 (UART_RXD)
unnamed: R36.2, U3.P$67 (UART_CTS)
unnamed: R37.2, U3.P$66 (UART_RTS)
NET_STATUS: R31.1, U3.P$51 (GPIO1); also elsewhere on the board
POWER_ON: Q2.3 (C), U3.P$3 (POWER_ON)
SIM_RESET: U3.P$18 (USIM_RESET); also elsewhere on the board
USIM_CLK: U3.P$19 (USIM_CLK); also elsewhere on the board
USIM_DATA: U3.P$17 (USIM_DATA); also elsewhere on the board
V_USIM: U3.P$20 (V_USIM); also elsewhere on the board

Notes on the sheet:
3G MODULE


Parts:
IC6: 24LC00OT; SOT23-5L
R40, R41: 2.2k; R0603

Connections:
+3V3: IC6.4 (VCC), R40.2, R41.2; also elsewhere on the board
GND: IC6.2 (GND); also elsewhere on the board
MEM_SCL: IC6.1 (SCL), R40.1; also elsewhere on the board
MEM_SDA: IC6.3 (SDA), R41.1; also elsewhere on the board

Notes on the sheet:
EEPROM



Board: 4 copper layers, 104.0 x 56.9 mm, 112 parts (26 on the bottom side), 75 nets.

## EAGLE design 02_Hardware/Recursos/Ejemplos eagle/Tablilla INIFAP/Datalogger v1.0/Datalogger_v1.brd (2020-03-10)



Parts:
BAT1: BATTERY20PTH; BATTCOM_20MM_PTH
C1, C2: 22pF; C0603K
C3, C4: 15pF; C0603K
C5, C6, C15, C16, C22, C39, C40: 1uF; C0805K
C7, C8, C9, C10, C12, C14, C21, C23, C24, C25, C26, C27, C28, C30, C31, C32, C33, C34, C35, C36, C37, C38: 0.1uF; C0805K
C11, C17, C29: 47uF; 153CLV-0605
C13, C41, C42: 10uF; C0805K
C18, C19: 10pF; C0603K
C20: 100pF; C0805K
IC1, IC2, IC5: MCP1703CB; SOT23
IC3, IC4: 4051D; SO16
J1, J2, J3, J4, J5: AUDIO-JACK2PTH; AUDIO-JACK
JP1: M02POLAR; MOLEX-1X2
JP2, JP3: PINHD-1X2; 1X02
JP4: M04POLAR; MOLEX-1X4
LED1, LED2, LED3, LED4, LED5, LED6, LED7: LEDCHIPLED_0603; CHIPLED_0603
Q1, Q4: CRYSTALMM20SS; MM20SS
Q2: CSM-7X-DU
Q3, Q5, Q6, Q7, Q8, Q9, Q10, Q11, Q12: 2N7000_SOT23; SOT-23
R1, R3, R5, R8, R9, R10, R11, R12, R13, R14: 10k; R0805
R2: 470; R0805
R4, R15, R16, R17, R18, R19, R20, R21: 1k; R0805
R6, R7: 2k; R0805
R23, R24, R25, R26, R27: 100k; R0805
S1: TAC_SWITCHSMD; TACTILE-SWITCH-SMD
S2, S3: SWITCH-SPDT-SMD-A; SWITCH-SPST-SMD-A
S4: DIP_SWITCH_8_POS_SMD; SWITCH_04
SV1: MA06-1
U1: PIC24FJXXXGCX06-X_PT; TQFP64_10X10MC
U2: SCHA4B0400
U3: MCP79410I/SN; SO8
U$1: XBEE-1B1; XBEE-1
U$2: ARDUINO_R3_SHIELDNOLABELS; UNO_R3_SHIELD_NOLABELS
X1: MINI-USB-UX60A-MB-5ST; UX60A-MB-5ST

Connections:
+3V3: C6.1, C7.1, C8.1, C9.1, C10.1, C11.+, C14.1, C21.1, C30.1, C31.1, C37.1, C41.1, IC1.2 (VO), IC3.16 (VCC), IC4.16 (VCC), R1.2, R6.1, R7.1, S3.3 (S), SV1.2, U1.10 (VDD_2), U1.19 (AVDD), U1.26 (SVDD), U1.35 (VUSB3V3), U1.38 (VDD), U2.VDD, U3.8 (VCC), U$2.3.3V
+5V: C16.1, C17.+, IC2.2 (VO), S3.1 (O), U$2.5V
AS_RESET: C12.1, R1.1, R2.2, S1.3, S1.4
BAT: C29.+, JP1.1, S2.1 (O)
CH0+: C28.1, IC3.3 (X), U1.22 (CH0+)
DATA+: U1.37 (D+/RG2), X1.3
DATA-: U1.36 (D-/RG3), X1.2
DIP_SW: IC4.3 (X), U1.33 (RF3), U$2.D13
GND: BAT1.2 (-), C1.2, C2.2, C3.2, C4.2, C5.2, C6.2, C7.2, C8.2, C9.2, C10.2, C11.-, C12.2, C13.2, C14.2, C15.2, C16.2, C17.-, C18.2, C19.2, C20.2, C21.2, C22.2, C23.2, C24.2, C25.2, C26.2, C27.2, C28.2, C29.-, C30.2, C31.2, C32.2, C33.2, C34.2, C35.2, C36.2, C37.2, C38.2, C39.2, C40.2, C41.2, C42.2, IC1.1 (GND), IC2.1 (GND), IC3.6 (INH), IC3.7 (VEE), IC4.6 (INH), IC4.7 (VEE), IC5.1 (GND), JP1.2, JP4.2, LED1.C, LED2.C, LED3.C, LED5.C, LED7.C, Q3.2 (S), Q5.2 (S), Q6.2 (S), Q7.2 (S), Q8.2 (S), Q9.2 (S), Q10.2 (S), Q11.2 (S), Q12.2 (S), R3.1, R5.1, R8.1, R9.1, R10.1, R11.1, R12.1, R13.1, R14.1, R23.1, R24.1, R25.1, R26.1, R27.1, S1.1, S1.2, S4.9, S4.10, S4.11, S4.12, S4.13, S4.14, S4.15, S4.16, SV1.3, U1.9 (VSS_2), U1.20 (AVSS), U1.21 (SVSS), U1.23 (CH0-), U1.41 (VSS), U$1.10 (GND), U$2.GND@0 (GND), U$2.GND@1 (GND), U$2.GND@2 (GND), X1.5
GSM_RX: U1.5 (RG7), U$2.D2
GSM_TX: U1.6 (RG8), U$2.D3 (*D3)
LED1: R15.2, U1.14 (RB2), U$2.D9 (*D9)
LED2: R16.2, U1.13 (RB3), U$2.D8
LED3: R17.2, U1.12 (RB4), U$2.D7
MCLR: R2.1, SV1.1, U1.7 (*MCLR)
MUX1_EN: Q11.1 (G), R13.2, U1.4 (RG6)
MUX2_EN: Q12.1 (G), R14.2, U1.11 (RB5), U$2.D10 (*D10)
MUX_A: IC3.11 (A), IC4.11 (A), U1.1 (RE5), U$2.D4
MUX_B: IC3.10 (B), IC4.10 (B), U1.2 (RE6), U$2.D5 (*D5)
MUX_C: IC3.9 (C), IC4.9 (C), U1.3 (RE7), U$2.D6 (*D6)
unnamed: C3.1, Q2.2, U1.40 (OSCO/RC15)
unnamed: C4.1, Q2.1, U1.39 (OSCI/RC12)
unnamed: C2.1, Q1.4 (2), U1.48 (RC14)
unnamed: C1.1, Q1.1, U1.47 (RC13)
unnamed: C15.1, IC2.3 (VI), JP2.1
unnamed: LED1.A, R15.1
unnamed: BAT1.1 (+), R4.2
unnamed: C18.1, Q4.1, U3.1 (X1)
unnamed: C13.1, U1.56 (VCAP)
unnamed: Q3.3 (D), U2.GND (VSS), U2.GND@1 (VSS), U2.GND@2 (VSS), U2.VSS
unnamed: C39.1, IC5.3 (VI), JP3.1
unnamed: C19.1, Q4.4 (2), U3.2 (X2)
unnamed: C20.1, R4.1, U3.3 (VBAT)
unnamed: Q5.3 (D), U3.4 (VSS)
unnamed: J1.SLEEVE, Q6.3 (D)
unnamed: IC4.8 (GND), Q12.3 (D)
unnamed: J2.SLEEVE, Q7.3 (D)
unnamed: C22.1, C32.1, C33.1, C34.1, C35.1, C36.1, J1.TIP, J2.TIP, J3.TIP, J4.TIP, J5.TIP, S3.2
unnamed: IC3.8 (GND), Q11.3 (D)
unnamed: J3.SLEEVE, Q8.3 (D)
unnamed: IC4.4 (X7), S4.1
unnamed: J4.SLEEVE, Q9.3 (D)
unnamed: IC4.2 (X6), S4.2
unnamed: J5.SLEEVE, Q10.3 (D)
unnamed: IC4.5 (X5), S4.3
unnamed: IC4.1 (X4), S4.4
unnamed: IC4.12 (X3), S4.5
unnamed: IC4.15 (X2), S4.6
unnamed: IC4.14 (X1), S4.7
unnamed: IC4.13 (X0), S4.8
unnamed: LED2.A, R16.1
unnamed: LED3.A, R17.1
unnamed: LED5.A, R19.2
unnamed: C38.1, C40.1, C42.1, IC5.2 (VO), LED4.A, LED6.A, U$1.1 (VDD)
unnamed: LED4.C, R18.2
unnamed: LED6.C, R20.2
unnamed: LED7.A, R21.2
unnamed: R21.1, U$1.13 (DIO9)
P1_CON: J1.TSH, R27.2, U1.54 (RD6)
P1_ON: Q6.1 (G), R8.2, U1.53 (RD5)
P2_CON: J2.TSH, R26.2, U1.58 (RF0)
P2_ON: Q7.1 (G), R9.2, U1.55 (RD7)
P3_CON: J3.TSH, R25.2, U1.60 (RE0)
P3_ON: Q8.1 (G), R10.2, U1.59 (RF1)
P4_CON: J4.TSH, R24.2, U1.62 (RE2)
P4_ON: Q9.1 (G), R11.2, U1.61 (RE1)
P5_CON: J5.TSH, R23.2, U1.63 (RE3)
P5_ON: Q10.1 (G), R12.2, U1.64 (RE4)
PORT1: C23.1, IC3.5 (X5), J1.RING, U1.46 (RD0), U$2.A0
PORT2: C24.1, IC3.15 (X2), J2.RING, U1.49 (RD1), U$2.A1
PORT3: C25.1, IC3.4 (X7), J3.RING, U1.50 (RD2), U$2.A2
PORT4: C26.1, IC3.2 (X6), J4.RING, U1.51 (RD3), U$2.A3
PORT5: C27.1, IC3.1 (X4), J5.RING, U1.52 (RD4), U$2.A4
RB6: SV1.5, U1.17 (RB6), U$2.D11 (*D11)
RB7: SV1.4, U1.18 (RB7), U$2.D12
RTC_ON: Q5.1 (G), R5.2, U1.27 (RB12)
RX2: JP4.3, R20.1, U1.15 (RB1), U$1.2 (DOUT)
SCK1: U1.31 (RF4), U2.CLK
SCL1: R7.2, U1.44 (RD10), U3.6 (SCL)
SDA1: R6.2, U1.43 (RD9), U3.5 (SDA)
SDI1: U1.29 (RB14), U2.MISO/DAT0
SDO1: U1.30 (RB15), U2.MOSI/CMD
SD_ON: Q3.1 (G), R3.2, U1.28 (RB13)
SS1: U1.32 (RF5), U2.!CS!/NC/DAT3 (!CS!/NC)
TX2: JP4.4, R18.1, U1.16 (RB0), U$1.3 (DIN)
VBAT: U1.57 (VBAT)
VBUS: R19.1, S2.3 (S), U1.34 (VBUS/RF7), X1.1
VIN: C5.1, IC1.3 (VI), JP2.2, JP3.2, JP4.1, S2.2, U$2.VIN

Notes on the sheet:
PICkit Programmer
3.3V Regulator
Reset button
USB Connection
Battery/USB Power select
BATTERY
5V Extra power source
MCU
MicroSD card
External RTCC
DATALOGGER V1.0 Creado por: Ing. Carlos Mendoza Enríquez Caracteristicas: -5 puertos de conexion para sensores. -Compatibilidad con sensores analogicos, digitales y de pulsos. -Compatibilidad con la gran mayoria de sensores marca Decagon Devices. Notas: (1) No todos los shields son compatibles con 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
Sensor ports
Sigma-Delta ADC Mux
General purpose DIP Switch
General purpose LEDs
Expansion
Arduino Shield compatibility (1)
XBee port with independent power supply


Board: 2 copper layers, 101.0 x 104.6 mm, 113 parts (0 on the bottom side), 87 nets.

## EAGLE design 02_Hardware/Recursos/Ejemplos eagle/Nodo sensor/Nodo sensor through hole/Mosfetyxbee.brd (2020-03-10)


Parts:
C1: CAP_POLPTH2; CPOL-RADIAL-10UF-25V
IC1: 4050N; DIL16
J1, J2, J3: AUDIO-JACK2PTH; AUDIO-JACK
LED1, LED2: LED3MM
Q1, Q2, Q3: 2N7000; TO-92
R1, R2, R3: 100k; 0207/12
R4, R5: 1k; 0207/10
U$1: XBEE-1B1; XBEE-1
U$2: ARDUINO_R3_SHIELDNOLABELS; UNO_R3_SHIELD_NOLABELS
X1, X2, X3: 22-23-2031

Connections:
unnamed: Q1.2 (G), R1.2, U$2.D5 (*D5)
unnamed: Q2.2 (G), R2.2, U$2.D6 (*D6)
unnamed: Q3.2 (G), R3.2, U$2.D7
unnamed: J1.SLEEVE, Q1.3 (D), X1.3
unnamed: J2.SLEEVE, Q2.3 (D), X2.3
unnamed: J3.SLEEVE, Q3.3 (D), X3.3
unnamed: C1.1 (+), IC1.1 (VDD), J1.TIP, J2.TIP, J3.TIP, R5.2, U$1.1 (VDD), U$2.3.3V, X1.1, X2.1, X3.1
unnamed: C1.2 (-), IC1.8 (VSS), LED1.K (C), LED2.K (C), Q1.1 (S), Q2.1 (S), Q3.1 (S), R1.1, R2.1, R3.1, U$1.10 (GND), U$2.GND@0 (GND)
unnamed: J1.RING, U$2.A2, X1.2
unnamed: J2.RING, U$2.A1, X2.2
unnamed: J3.RING, U$2.A0, X3.2
unnamed: IC1.3 (I), U$2.TX
unnamed: IC1.2 (O), U$1.3 (DIN)
unnamed: U$1.2 (DOUT), U$2.RX
unnamed: R4.2, U$1.13 (DIO9)
unnamed: LED1.A, R4.1
unnamed: LED2.A, R5.1


Board: 2 copper layers, 55.9 x 74.6 mm, 20 parts (0 on the bottom side), 17 nets.

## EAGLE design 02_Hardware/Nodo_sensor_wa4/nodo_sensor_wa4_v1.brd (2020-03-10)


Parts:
ARD1: ARDUINO_MKR
JP1: XBEE
J_BT_BOARD_1: BLUETOOTH_BOARD; BT_BOARD_FOOTPRINT
LED1, LED2: LEDCHIP-LED0805; CHIP-LED0805
Q5: BCX70SMD; SOT23
R1, R36: 330; R0805
R2, R3: 10k; R0805
U$1: JST-4

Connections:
+3V3: JP1.1 (VDD), J_BT_BOARD_1.VCC, R1.2, R36.2, U$1.3; also elsewhere on the board
+5V: ARD1.28 (5V); also elsewhere on the board
BT_RX: ARD1.23 (14/TX), J_BT_BOARD_1.RX
BT_TX: ARD1.22 (13/RX), J_BT_BOARD_1.TX
GND: ARD1.25 (GND), JP1.10 (GND), J_BT_BOARD_1.GND, LED1.C, Q5.2 (E), R3.1, U$1.4; also elsewhere on the board
GPS_SCL: ARD1.21 (12/SCL), U$1.1
GPS_SDA: ARD1.20 (11/SDA), U$1.2
IN_LED2_ON: ARD1.5 (A3), R2.1
unnamed: LED2.A, R36.1
unnamed: LED2.C, Q5.3 (C)
unnamed: LED1.A, R1.1
unnamed: Q5.1 (B), R2.2, R3.2
S1_INPUT: ARD1.6 (A4); also elsewhere on the board
S1_ON: ARD1.13 (~4); also elsewhere on the board
S2_INPUT: ARD1.7 (A5); also elsewhere on the board
S2_ON: ARD1.14 (~5); also elsewhere on the board
S3_INPUT: ARD1.8 (A6); also elsewhere on the board
S3_ON: ARD1.15 (6); also elsewhere on the board
S4_INPUT: ARD1.12 (~3); also elsewhere on the board
S4_ON: ARD1.16 (7); also elsewhere on the board
S5_INPUT: ARD1.10 (1); also elsewhere on the board
S5_ON: ARD1.19 (10/MISO); also elsewhere on the board
S6_INPUT: ARD1.3 (A1); also elsewhere on the board
XB_RX: ARD1.17 (8/MOSI), JP1.3 (DIN)
XB_TX: ARD1.18 (9/SCK), JP1.2 (DOUT)

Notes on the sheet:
ARDUINO & COM

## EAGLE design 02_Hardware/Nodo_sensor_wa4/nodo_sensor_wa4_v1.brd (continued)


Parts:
C3, C4, C5, C6, C7: 0.1uF; C0805
Q1, Q2, Q3, Q4, Q6: 5.8A/30V/35mΩ; SOT23-3
R4, R5, R6, R7, R8, R9: 10k; R0805
X1, X2, X3, X4, X5, X6: 35RAPC2BH3

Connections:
+3V3: C3.1, C4.1, C5.1, C6.1, C7.1, R9.2, X1.4 (5), X1.5, X2.4 (5), X2.5, X3.4 (5), X3.5, X4.4 (5), X4.5, X5.4 (5), X5.5; also elsewhere on the board
GND: Q1.2 (S), Q2.2 (S), Q3.2 (S), Q4.2 (S), Q6.2 (S), R4.1, R5.1, R6.1, R7.1, R8.1, X6.1; also elsewhere on the board
unnamed: C3.2, Q1.3 (D), X1.1
unnamed: C4.2, Q2.3 (D), X2.1
unnamed: C5.2, Q3.3 (D), X3.1
unnamed: C6.2, Q4.3 (D), X4.1
unnamed: C7.2, Q6.3 (D), X5.1
S1_INPUT: X1.2, X1.3 (2); also elsewhere on the board
S1_ON: Q1.1 (G), R4.2; also elsewhere on the board
S2_INPUT: X2.2, X2.3 (2); also elsewhere on the board
S2_ON: Q2.1 (G), R5.2; also elsewhere on the board
S3_INPUT: X3.2, X3.3 (2); also elsewhere on the board
S3_ON: Q3.1 (G), R6.2; also elsewhere on the board
S4_INPUT: X4.2, X4.3 (2); also elsewhere on the board
S4_ON: Q4.1 (G), R7.2; also elsewhere on the board
S5_INPUT: X5.2, X5.3 (2); also elsewhere on the board
S5_ON: Q6.1 (G), R8.2; also elsewhere on the board
S6_INPUT: R9.1, X6.2, X6.3 (2); also elsewhere on the board

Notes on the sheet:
SENSORES


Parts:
C1: 0.33uF; C0805
C2: 0.1uF; C0805
U2: UA78M33; UA78XX

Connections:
+3V3: C2.1, U2.OUT; also elsewhere on the board
+5V: C1.1, U2.IN; also elsewhere on the board
GND: C1.2, C2.2, U2.COM (GND); also elsewhere on the board

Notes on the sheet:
FUENTES
3.3V SUPPLY


Board: 2 copper layers, 166.0 x 110.0 mm, 36 parts (0 on the bottom side), 30 nets.

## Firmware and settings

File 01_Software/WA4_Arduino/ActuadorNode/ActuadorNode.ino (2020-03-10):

 
 /*===================================================================================================================================*/
/*=====                                          Sensor node firmware v4.0                                                      =====*/
/*=====                                                   ARDUINO Mega                                                           =====*/
/*=====                                              Water Automation                                                           =====*/
/*=====                                                                                                                         =====*/
/*=====                                                                                                                         =====*/
/*=====                                                                                                                         =====*/
/*===================================================================================================================================*/

/*----------Variables de configuracion-------------*/
int standalone=1; // 1-standalone, 0-Zigbee comm

// Define output locations
#define VALVE1_ON   digitalWrite(7, HIGH)
#define VALVE1_OFF  digitalWrite(7, LOW)
#define VALVE2_ON   digitalWrite(6, HIGH)
#define VALVE2_OFF  digitalWrite(6, LOW)
#define VALVE3_ON   digitalWrite(5, HIGH)
#define VALVE3_OFF  digitalWrite(5, LOW)
#define LED1_ON     digitalWrite(9, HIGH)
#define LED1_OFF    digitalWrite(9, LOW)
#define LED2_ON     digitalWrite(10, HIGH)
#define LED2_OFF    digitalWrite(10, LOW)
#define LED3_ON     digitalWrite(11, HIGH)
#define LED3_OFF    digitalWrite(11, LOW)
  
// declare global variables
 char bufferin[80];
 unsigned char buffout[80];
 char serial_cmd[10];
 char valve1_status;
 char valve2_status;
 char valve3_status;

 unsigned char battery_level = 0xFF;
 unsigned char pressure_units = 0x42;
 int sum;
 unsigned char pressure_decimals = 0x42;
 float discharge2 =0;
 float discharge =0;


 unsigned long tiempoanterior;
 unsigned long tiempo=60000; //time for discharge calc
 unsigned long flow_counter = 0;
 int i = 0;
 
char input_message_size=22;
char output_message_size=32;

//---------------------------------------------------------
// Set-up function
//--------------------------------------------------------- 
void setup(){
 
   pinMode(9, OUTPUT); //LED 1
   pinMode(10, OUTPUT);//LED 2
   pinMode(11, OUTPUT);//LED 3
   pinMode(6, OUTPUT); //VALVE 2
   pinMode(7, OUTPUT); //VALVE 1
   pinMode(5, OUTPUT); //VALVE 3
   attachInterrupt(0, flow, RISING);
   Serial.begin(9600);

   for(int j=0; j<255 ; j++) {analogWrite(9,j); delay(2);}
   for(int j=255; j>=0 ; j--) {analogWrite(9,j); delay(2);}
   for(int j=0; j<255 ; j++) {analogWrite(10,j); delay(2);}
   for(int j=255; j>=0 ; j--) {analogWrite(10,j); delay(2);}
   for(int j=0; j<255 ; j++) {analogWrite(11,j); delay(2);}
   for(int j=255; j>=0 ; j--) {analogWrite(11,j); delay(2);}
   
  digitalWrite(7, HIGH);
  digitalWrite(9, HIGH);
  delay(300);
  digitalWrite(7, LOW);
  digitalWrite(9, LOW);
  delay(300);
  digitalWrite(6, HIGH);
  digitalWrite(10, HIGH);
  delay(300);
  digitalWrite(6, LOW);
  digitalWrite(10, LOW);
  delay(300);
  digitalWrite(5, HIGH);
  digitalWrite(11, HIGH);
  delay(300);
  digitalWrite(5, LOW);
  digitalWrite(11, LOW);
  delay(300);
 }
 
//---------------------------------------------------------
// Main loop
//---------------------------------------------------------
void loop(){
  
 if(valve1_status == 1) LED1_ON;
 else LED1_OFF;
 
 if(valve2_status == 1) LED2_ON;
 else LED2_OFF;
 
 if(valve3_status == 1) LED3_ON;
 else LED3_OFF;

 unsigned long tiempoactual=millis();
  
 if(tiempoactual - tiempoanterior > tiempo) {         
          discharge_calc(flow_counter);  
          if( standalone==1){
              Serial.println("-------------");
              Serial.println("FLOW SENSOR");
              Serial.println("-------------");
              Serial.print("Flow Counter: ");
              Serial.println(flow_counter,DEC);
              Serial.print("Discharge: ");
              Serial.println(discharge,2);
              Serial.print("Discharge2: ");
              Serial.println(discharge2,2);
           }
          flow_counter = 0;
          tiempoanterior = tiempoactual; 
 }
}
 
//---------------------------------------------------------
// Process Xbee message and send a response
//---------------------------------------------------------
void serialEvent(){
  char serial_cmd[11];
  i = 0;
  if( standalone==0){
    if(Serial.available()>0){  
      Serial.readBytes(bufferin,input_message_size);
      if(bufferin[0] == 0x7E && bufferin[15]== 'A'){
          if(bufferin[16] == '1') {valve1_status = 1; VALVE1_ON; }
          else if(bufferin[16] == '0'){valve1_status = 0; VALVE1_OFF;}
          if(bufferin[17] == '1') {valve2_status = 1; VALVE2_ON; }
          else if(bufferin[17] == '0'){valve2_status = 0; VALVE2_OFF;}
          if(bufferin[18] == '1') {valve3_status = 1; VALVE3_ON; }
          else if(bufferin[18] == '0'){valve3_status = 0; VALVE3_OFF;}
           
          buffout[0]=0x7E;//API mode start delimeter
          buffout[1]=0x00;//Data length MSB
          buffout[2]=output_message_size-4;//Data length LSB
          buffout[3]=0x10;//API ID TX Request 16 bit address
          buffout[4]=0x00;//Frame ID, if equals to 0x00 disable response frame
          buffout[5]=bufferin[4];
          buffout[6]=bufferin[5];
          buffout[7]=bufferin[6];
          buffout[8]=bufferin[7];
          buffout[9]=bufferin[8];
          buffout[10]=bufferin[9];
          buffout[11]=bufferin[10];
          buffout[12]=bufferin[11];//Destination Address LSB
          buffout[13]=0xFF;
          buffout[14]=0xFE;
          buffout[15]=0x00;
          buffout[16]=0x00;
          buffout[17]='A'; 
          buffout[18]=valve1_status;
          buffout[19]=valve2_status;
          buffout[20]=valve3_status;
          buffout[21]=highByte((unsigned int)(discharge*100));  //Water Flow liters/minute 
          buffout[22]=lowByte((unsigned int)(discharge*100));  //Water Flow liters/minute 
          buffout[23]=0x00;
          buffout[24]=0x00;
          buffout[25]=0x00;
          buffout[26]=0x00;
          buffout[27]=0x00;
          buffout[28]=0x00;
          buffout[29]=0x00;
          buffout[30]=0x0A;//End of package
          for(int i=3;i<output_message_size-1;i++){
               sum+=buffout[i]; //Checksum
          }
          buffout[31]=0xFF-lowByte(sum);
          sum=0;
          Serial.write(buffout,output_message_size);      
       }
    }
 }
 else{
      char v1,v2,v3;
      v1=Serial.read();
      delay(100);
      v2=Serial.read();
      delay(100);
      v3=Serial.read();
      delay(100);
      if(v1 == '1') {valve1_status = 1; VALVE1_ON; }
      else if(v1 == '0'){valve1_status = 0; VALVE1_OFF;}
      if(v2 == '1') {valve2_status = 1; VALVE2_ON; }
      else if(v2 == '0'){valve2_status = 0; VALVE2_OFF;}
      if(v3 == '1') {valve3_status = 1; VALVE3_ON; }
      else if(v3 == '0'){valve3_status = 0; VALVE3_OFF;}
      Serial.println("-------------");
      Serial.println("ACTUATOR NODE");
      Serial.println("-------------");
      Serial.print("Valve 1: ");
      Serial.println(valve1_status,DEC);
      Serial.print("Valve 2: ");
      Serial.println(valve2_status,DEC);
      Serial.print("Valve 3: ");
      Serial.println(valve3_status,DEC);
  }
}
 
//---------------------------------------------------------
// Count pulses from flow sensor
//---------------------------------------------------------
void flow(){
   digitalWrite(11, HIGH);
   delay(20);
   flow_counter++;
   digitalWrite(11, LOW);
}
 

//---------------------------------------------------------
// Calculate water consumption from pulses
//---------------------------------------------------------
void discharge_calc(unsigned long pulses){
  
  #define offset 0.39
  #define K 0.44
  #define fact_litres 3.78541
 
  if (pulses > 10){
      // Liters = 0.0407*pulses +2.7478 
      discharge = (0.0407*pulses) + 2.7478;// Linear approximation formula
      //Datasheet formula
      discharge2 = (((float)pulses/60) + offset)*K;  // in gallons per minute
      discharge2 = discharge2*fact_litres;
      // 530 pulses = 20 lts = 5.28344 gallons
      //1003 pulses = 10 gallons
  }
  else{
      discharge = 0;  
      discharge2 = 0;
  }  
}

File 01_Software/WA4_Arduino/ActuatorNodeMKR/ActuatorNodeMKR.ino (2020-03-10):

/*========================================================================*/
/*=====                   Actuator node firmware v4.0                       */
/*=====                          ARDUINO MKR                              */
/*=====                        Water Automation                           */
/*=====                                                                   */
/*=====     To power LED2 use 10 as a digital output                      */
/*========================================================================*/


#include <math.h>
#include <Arduino.h>        // required before wiring_private.h
#include "wiring_private.h" // pinPeripheral() function
#include <jm_PCF8574.h>
#include <Wire.h>
#include <string.h>
#include "PeriodicTask.h"

/*=====Optional hardware=====*/
#define FSEN5_ENABLE        false
/*===========================*/

/*=====Arduino definitions=====*/
#define NODE_TYPE           'A'
#define LED_SIGNAL          10  // A3 as an indicator led
#define SAMPLING_PERIOD     60  //Sampling period in seconds 
#define TIME_OFFSET         10  //Time Offset to execute first measurement in seconds

#define FSEN1_SIGNAL        A1  //Flow sensor 1 INPUT pin
#define FSEN2_SIGNAL        A2  //Flow sensor 2 INPUT pin
#define FSEN3_SIGNAL         0  //Flow sensor 3 INPUT pin
#define FSEN4_SIGNAL         1  //Flow sensor 4 INPUT pin
#define FSEN5_SIGNAL         4  //Flow sensor 5 INPUT pin

#define VALV1_SIGNAL        A4
#define VALV2_SIGNAL        A3
#define VALV3_SIGNAL        A6
#define VALV4_SIGNAL        A5

#define PUMP_ON_SIGNAL       2
#define PUMP_OFF_SIGNAL      3

#define expinMode(a,b)        PCF8574.pinMode(a,b)
#define exdigitalWrite(a,b)   PCF8574.digitalWrite(a,b)
#define exdigitalRead(a)      PCF8574.digitalRead(a)


#define VALV1_FB_SIGNAL     ((uint8_t) 7)  // I/O Expansion chip P7
#define VALV3_FB_SIGNAL     ((uint8_t) 6)  // I/O Expansion chip P7
#define VALV2_FB_SIGNAL     ((uint8_t) 5)  // I/O Expansion chip P7
#define VALV4_FB_SIGNAL     ((uint8_t) 4)  // I/O Expansion chip P7
#define VALV4_CLR_SIGNAL    ((uint8_t) 3)  // I/O Expansion chip P7
#define VALV3_CLR_SIGNAL    ((uint8_t) 2)  // I/O Expansion chip P7
#define VALV2_CLR_SIGNAL    ((uint8_t) 1)  // I/O Expansion chip P7
#define VALV1_CLR_SIGNAL    ((uint8_t) 0)  // I/O Expansion chip P7

#define VALV1_STATE()   exdigitalRead(VALV1_FB_SIGNAL)
#define VALV2_STATE()   exdigitalRead(VALV2_FB_SIGNAL)
#define VALV3_STATE()   exdigitalRead(VALV3_FB_SIGNAL)
#define VALV4_STATE()   exdigitalRead(VALV4_FB_SIGNAL)

#define VALV1_CLR_ON()  exdigitalWrite(VALV1_CLR_SIGNAL, HIGH)
#define VALV2_CLR_ON()  exdigitalWrite(VALV2_CLR_SIGNAL, HIGH)
#define VALV3_CLR_ON()  exdigitalWrite(VALV3_CLR_SIGNAL, HIGH)
#define VALV4_CLR_ON()  exdigitalWrite(VALV4_CLR_SIGNAL, HIGH)

#define VALV1_CLR_OFF()  exdigitalWrite(VALV1_CLR_SIGNAL, LOW)
#define VALV2_CLR_OFF()  exdigitalWrite(VALV2_CLR_SIGNAL, LOW)
#define VALV3_CLR_OFF()  exdigitalWrite(VALV3_CLR_SIGNAL, LOW)
#define VALV4_CLR_OFF()  exdigitalWrite(VALV4_CLR_SIGNAL, LOW)

#define VALV1_ON()    digitalWrite(VALV1_SIGNAL, HIGH)
#define VALV2_ON()    digitalWrite(VALV2_SIGNAL, HIGH)
#define VALV3_ON()    digitalWrite(VALV3_SIGNAL, HIGH)
#define VALV4_ON()    digitalWrite(VALV4_SIGNAL, HIGH)

#define VALV1_OFF()   digitalWrite(VALV1_SIGNAL, LOW)
#define VALV2_OFF()   digitalWrite(VALV2_SIGNAL, LOW)
#define VALV3_OFF()   digitalWrite(VALV3_SIGNAL, LOW)
#define VALV4_OFF()   digitalWrite(VALV4_SIGNAL, LOW)


#define TURN_ON_LED()       digitalWrite(LED_SIGNAL,HIGH)
#define TURN_OFF_LED()      digitalWrite(LED_SIGNAL,LOW)
/*=============================*/

/*====Periodic tasks prototypes====*/
void flowCalcTask(void);
/*===================================*/

/*=====Debug mode=====*/
bool DEBUG_MODE = true;
/*====================*/

/*=====Timer variables=====*/
unsigned long previousMillis;
unsigned long timeInterval;
unsigned long sequence = 0;
int debugMode = 1;
/*=========================*/


/*=====Communication variables=====*/
char input_message_size = 23;
char output_message_size = 41;
char Buffout[80], Buffin[80];
/*=================================*/

/*===========Flow variables===========*/
volatile unsigned long flowCounter1 = 0;
volatile unsigned long flowCounter2 = 0;
volatile unsigned long flowCounter3 = 0;
volatile unsigned long flowCounter4 = 0;
volatile unsigned long flowCounter5 = 0;
volatile float discharge1 = 0;
volatile float discharge2 = 0;
volatile float discharge3 = 0;
volatile float discharge4 = 0;
volatile float discharge5 = 0;
unsigned const long flowInterval = 60000;
/*====================================*/

/*===========Pump variables===========*/
unsigned const long pumpInterval = 1000;
/*====================================*/

/*=============I/O Expansion chip===============*/
#define PCF8574_ADDR1  ((uint8_t) 0x20)    // default PCF8574 I2C address
#define PCF8574_ADDR2  ((uint8_t) 0x21)    // alternative PCF8574 I2C address

jm_PCF8574 PCF8574;
/*==============================================*/
/*=====Re-usable class for periodic timed tasks=====*/

/*==================================================*/

/*=============Periodic tasks declaration==============*/
PeriodicTask flowTask(flowInterval, &FLOW_TASK);
PeriodicTask pumpTask(pumpInterval, &PUMP_TASK);
/*=====================================================*/
//---------------------------------------------------------
// Create the new UART instance for Xbee communication assigning it to pin 8(TX) and 9(RX)
//---------------------------------------------------------
//Uart SerialXbee(&sercom1, 8, 9, SERCOM_RX_PAD_1, UART_TX_PAD_0);


void setup() {

  Serial.begin(115200);   // Configure USB serial as serial monitor
  //while (!Serial);
  Serial1.begin(9600);  // Configure Pins 13(RX),14(TX) for Bluetooth communication
  while (!Serial1);

  //SerialXbee.begin(9600); // Configure Pins 8(TX),9(RX) for Xbee communication
  //while (!SerialXbee);
  //pinPeripheral(8, PIO_SERCOM);
  //pinPeripheral(9, PIO_SERCOM);

  //PCF8574 Initialization
  Wire.begin();
  if (!PCF8574.begin(PCF8574_ADDR1)) {
    Serial.println("Failed to initialize I/O expansion chip. Trying alternative address...");
    if (!PCF8574.begin(PCF8574_ADDR2)) {
      Serial.println("Failed to initialize I/O expansion chip.");
    }
    else {
      Serial.println("I/O expansion chip init successfull with alternative address.");
    }
  }
  else {
    Serial.println("I/O expansion chip init successfull with default address.");
  }


  initPinConfig();
  initISR();

  //Initial state of valves and pump
  clearValves();
  PUMP_OFF();


  delay(1000);
  initialSequence();
  Serial.println("Initialization completed!!!");
}

void loop() {

  flowTask.RunHandler();
  pumpTask.RunHandler();
  //if(SerialXbee.available()){
  if(Serial1.available()){
    xbeeHandler();
  }
  serialCommandHandler();
}
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

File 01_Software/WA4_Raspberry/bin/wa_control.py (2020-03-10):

#!/usr/bin/env python

import serial
import array
import datetime
import wa_config_data
import csv

#---------------------------------------------------------------
# Calculate Kalman value
#---------------------------------------------------------------
def data_fusion(data):

        if data.sm_sensors==0b001:
                data.smC=data.sm1
                if data.verbose:
                        print("    Fusion (SM1)={0:5.2f}".format(data.smC))
        elif data.sm_sensors==0b010:
                data.smC=data.sm2
                if data.verbose:
                        print("    Fusion (SM2)={0:5.2f}".format(data.smC))
        elif data.sm_sensors==0b100:
                data.smC=data.sm3
                if data.verbose:
                        print("    Fusion (SM3)={0:5.2f}".format(data.smC))
        elif data.sm_sensors==0b011:
                data.smC=(data.sm1+data.sm2)/2.0
                if data.verbose:
                        print("    Fusion (SM1,SM2)={0:5.2f}".format(data.smC))
        elif data.sm_sensors==0b110:
                data.smC=(data.sm2+data.sm3)/2.0
                if data.verbose:
                        print("    Fusion (SM2,SM3)={0:5.2f}".format(data.smC))
        elif data.sm_sensors==0b101:
                data.smC=(data.sm1+data.sm3)/2.0
                if data.verbose:
                        print("    Fusion (SM1,SM3)={0:5.2f}".format(data.smC))
        elif data.sm_sensors==0b111:
                data.smC=(data.sm1+data.sm2+data.sm3)/3.0
                if data.verbose:
                        print("    Fusion (SM1,SM2,SM3)={0:5.2f}".format(data.smC))
        else:
                data.smC=0;
                print("    ERROR: NO DATA FUSION")

        if data.Q==0.0 or data.R==0.0:
                print("    NO KALMAN FILTER");
        else:        
                calculate_kalman(data)
        return 

#---------------------------------------------------------------
# Calculate Kalman value
#---------------------------------------------------------------
def calculate_kalman(data):

        k=(data.p1_ant+data.Q)/(data.p1_ant+data.Q+data.R)
        data.smC=data.smKalman_ant+k*(data.smC-data.smKalman_ant)
        p1=(data.p1_ant+data.Q)*(1-k)
        data.p1_ant=p1
        data.smKalman_ant=data.smC
        print("    ETo={0:5.2f}".format(data.w_eto));
        print("    SM_fusion={0:5.2f}".format(data.smC));
        return 


#---------------------------------------------------------------
# Verify constraints to activate irrigation
#---------------------------------------------------------------
def verify_constraints(data):

        if data.verbose:
                print('    VERIFYING CONSTRAINTS...')
                print('        Current irrigation area: '+str(data.area_id))

        for other_area in range(1, data.total_areas+1):
                if other_area != data.area_id:
                        file_name='../config/config_area'+str(other_area)+'.csv'
                        if data.verbose:                        
                                print('        Analyzing file: '+file_name)
                        with open(file_name) as csvfile:
                                readCSV=csv.reader(csvfile, delimiter='=')
                                for row in readCSV:
                                        if row[0]== 'valve_status':
                                                other_valve_status=int(row[1])
                                                if data.verbose:
                                                        print('        Valve Status: '+str(other_valve_status))
                                                if other_valve_status==1:
                                                        if data.verbose:
                                                                print('        CONSTRAINT: Irrigation area '+str(other_area)+' is active')
                                                        return False
                                csvfile.close()

        if data.verbose:
                print('        No constraint for irrigation')

        return True

#---------------------------------------------------------------
# Control algorithm
#---------------------------------------------------------------
def control_algorithm(data):

        if data.operation_mode=='auto':

                print('    Control algorithm in AUTO mode')
                if verify_constraints(data):
                        if wa_config_data.read_limits_file(data.limits_file,data.smC,data.valve_status,data.verbose):
                                data.valve_status=1;
                                print("    Valve status ({0:d})".format(data.valve_status));
                        else:
                                data.valve_status=0;
                                print("    Valve status ({0:d})".format(data.valve_status));                        
                        return
                else:
                        print('    No action since there is a constraint')
        
        elif data.operation_mode=='sched':

                print('    Control algorithm in SCHED mode')
                if verify_constraints(data):
                        c_weekday=datetime.datetime.today().weekday()
                        c_hour=datetime.datetime.today().hour
                        c_min=datetime.datetime.today().minute  
                        if wa_config_data.read_schedule_file(data.sched_file,c_weekday,c_hour,c_min):
                                data.valve_status=1;
                                print("    Valve status ({0:d})".format(data.valve_status));
                        else:
                                data.valve_status=0;
                                print("    Valve status ({0:d})".format(data.valve_status));
                        return
                else:
                        print('    No action since there is a constraint')

        elif data.operation_mode=='manual':

                print('    Control algorithm in MANUAL mode')
                if verify_constraints(data):
                        if wa_config_data.read_manual_control_file(data.manual_control_file):
                                data.valve_status=1;
                                print("    Valve status ({0:d})".format(data.valve_status));
                        else:
                                data.valve_status=0;
                                print("    Valve status ({0:d})".format(data.valve_status));
                        return
                else:
                        print('    No action since there is a constraint')

        else:
                print('    Control algorithm NOT-DEFINED mode')
                return
                
                

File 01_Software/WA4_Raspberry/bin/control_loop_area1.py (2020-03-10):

#!/usr/bin/env python

import wa_xbee_comm
import wa_config_data
import wa_control
import wa_iot_comm


#---------------------------------------------------------------
# Define data strcutures
#---------------------------------------------------------------
class irrigation_area:
        def __init__(self, id=0):
                self.area_id=id
                self.total_areas=4
                self.operation_mode='none'   #Options: none,manual,sched,auto
                self.config_file='../config/config_area'+str(id)+'.csv'
                self.sched_file='../config/sched_area'+str(id)+'.csv'
                self.manual_control_file='../config/manual_control_area'+str(id)+'.csv'
                self.operation_mode_file='../config/operation_mode_area'+str(id)+'.csv'
                self.limits_file='../config/limits_area'+str(id)+'.csv'
                self.log_file='../www/html/wa4_log/log_area'+str(id)+'.csv'
                self.data_file='../data/data_area'+str(id)+'.csv'
                self.verbose=0

                Q=0.0
                R=0.0
                p1_ant=1.0
                smKalman_ant=0.0
                smC=0.0
                sm1=0.0
                sm2=0.0
                sm3=0.0
                sm_sensors=0
                sm_actuators=0
                sensor_mac_address=bytearray()
                actuator_mac_address=bytearray()
                weather_mac_adress=bytearray()
                ndvi_mac_adress=bytearray()
                valve_status=0
                valve_flow=0.0
                altitude=1440
                w_radiation=0.0
                w_temperature=0.0
                w_humidity=0.0
                w_wind=0.0
                w_eto=0.0
                ndvi_alpha=0.0
                ndvi_value=0.0
                ndvi_red=0.0
                ndvi_nir=0.0
                error_code=0
                comm_status=0
                
                

#---------------------------------------------------------------
# Main program
#---------------------------------------------------------------
area1=irrigation_area(1)
print("IRRIGATION AREA 1")

if area1.verbose:
        print("(1) Read configuration files")
wa_config_data.read_config_file(area1.config_file,area1)
wa_config_data.read_operation_mode_file(area1.operation_mode_file,area1)
if area1.verbose:
        print("    OPERATION MODE: "+area1.operation_mode)

if area1.verbose:
        print("(2) Configure serial port")
ser = wa_xbee_comm.config_xbee_comm('/dev/ttyS0',9600)

if area1.verbose:
        print("(3) Transmit message to weather node")
for i in range(3): 
        wa_xbee_comm.transmit_weather_message(ser,area1,'WEATHER')
        wa_xbee_comm.receive_weather_message(ser,area1,'WEATHER')
        if area1.comm_status:
                break
        else:
                print("    Communication retry....");

if area1.verbose:
        print("(4) Transmit message to sensor node")
for i in range(3): 
        wa_xbee_comm.transmit_sensor_message(ser,area1,'S1')
        wa_xbee_comm.receive_sensor_message(ser,area1,'S1')
        if area1.comm_status:
                break
        else:
                print("    Communication retry....");

if area1.comm_status:

        if area1.verbose:
                print("(5) Calculate control action")
        wa_control.data_fusion(area1)
        wa_control.control_algorithm(area1)

        if area1.verbose:
                print("(6) Transmit control action to actuator")
        for i in range(3): 
                wa_xbee_comm.transmit_actuator_message(ser,area1,'ACTUATOR')
                wa_xbee_comm.receive_actuator_message(ser,area1,'ACTUATOR')
                if area1.comm_status:
                        break
                else:
                        print("    Communication retry....");

else:
        if area1.verbose:
                print("(5) No control action due SM data not available")
                print("(6) No action transmit to actuator due SM data not available")
        
        
if area1.verbose:
        print("(7)Update configuration file")
wa_config_data.update_config_file(area1.config_file,area1)

if area1.verbose:
        print("(8)Update data file")
wa_config_data.update_data_file(area1.data_file,area1)

if area1.verbose:
        print("(9)Update log file")
wa_config_data.update_log_file(area1.log_file,area1)
	
if area1.verbose:
        print("(10)Upload Data to ThingSpeak")
wa_iot_comm.update_thingspeak_area1(area1)

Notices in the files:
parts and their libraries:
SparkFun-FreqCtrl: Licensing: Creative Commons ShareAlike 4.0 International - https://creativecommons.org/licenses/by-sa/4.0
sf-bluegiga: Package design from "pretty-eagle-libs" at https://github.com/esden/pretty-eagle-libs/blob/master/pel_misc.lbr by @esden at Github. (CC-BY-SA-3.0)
